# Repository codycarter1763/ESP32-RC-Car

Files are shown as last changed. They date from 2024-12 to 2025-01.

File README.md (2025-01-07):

# DIY ESP32 RC Car

<p align="center">
  
</p>

<h1>Introduction</h1>
Using skills we gained through EE 3752 labs and lectures, my partner and I decided to apply our arm assembly knowledge to microcontrollers and create a fully functional RC car and controller powered by the ESP32. This project connects to ARM assembly and microprocessors by applying embedded system principles like GPIO/ADC handling, I/O, and real time communication. Skills we used in the labs including registers, loops, low-level debugging, and I/O helped us design and fabricate a functional project using the ESP32. This project is very important because it allowed us to take what we learned in class, and apply to a real world application. This connection is like what one would see in a job where you must think outside of the box using your technical skills to solve an issue. 

<h1>Background Information and Design Process</h1>
When we decided to take on this project, we started researching and deciding on what we need to make the RC car reliable, low cost, and fully functional. We chose the ESP32 microcontroller as our processor due to low cost, form factor, adaptability, and Bluetooth and Wi-Fi capabilities. The Xtensa dual-core 32-bit LX6 microprocessor, operating at 240 MHz adds a lot of capability compared to a normal Arduino UNO. The ESP32 also includes peripherals we need without having to buy WI-FI/Bluetooth modules to interface between the car and transmitter externally.

<p align="center">
  
</p>
<!-- -->
Our first iteration of the prototype involved a toy RC car kit on Amazon for our base. 
<p align="center">
  
</p>

Our goal was to have a finished RC car kit that we can place all our electronics on so we would not have to design a chassis. To get this iteration working, we would have to buy an ESP32, and two H-bridge motor drivers for steering and throttle. For the controller we wanted to use a phone app and use ESP32’s Bluetooth capability to control the RC car. This iteration would have worked fine for the scope of this project, but after seeing how fast we would finish the project we came up with a new idea. We wanted to take the RC car a step further and make a faster, more durable, and more custom RC car with a fabricated controller. 
<!-- -->
After research on Thingiverse, we settled on the platform called Carduino V2 and applied our own electronic design using the ESP32 Microcontroller and a brushless motor system. This design did not include any code files so this made it a perfect opportunity to design a system from scratch.

<p align="center">
  
</p>

With the use of a personal 3D printer, we were able to fabricate our own parts without relying on our college’s printers. 
<!-- -->
When we started developing this prototype, we first had trouble with the brushless motor and ESC interface with the ESP32 board. Getting a signal going to the ESC was tricky, the motor would power on and begin beeping in 1 second intervals. Per the instructions for the motor indicated to us that it wasn’t receiving a control signal from the board. Further troubleshooting indicated that the problem was the ESC was waiting for certain throttle calibration steps involving full, low, and neutral throttle. Once we built that functionality into our code, we were able to interface and control the ESC. Thankfully, the steering servo worked right away, it gave us no issues since no calibration is needed. 

<h1>Parts List</h1>
•	2x ESP32<br>
•	1000kv A2212 Brushless Motor 30 amp ESC combo<br>
•	2s 7.4 Volt LIPO<br>
•	SG90 Servos<br>
•	8x12x3.5 Bearings<br>
•	A959 Tire<br>
•	Screws<br>
•	Joysticks and Wires<br>
•	Headers<br>
•	2x Blue LEDs<br>
•	100 Ohm resistor<br>
•	2x Clear White LEDs (For Headlights)<br>
•	68 Ohm resistor<br>

<h1>Chassis Construction</h1>
Chassis construction was relatively simple, the instructions provided with the Carduino 3Dprint files were fairly thorough. The build was broken down into 3 sections; base, steering rack, and rear assembly. <br>
<br>
The rear assembly went together first, this component holds in 4 bearings which support the rear axle and reduce friction when its powered. The brushless motor sits on a mount above the rear assembly, it powers a gear that connects to the rear axle providing motion for the vehicle. The entire construction is held together by 20 M3x10 screws. The rear assembly also supports the wing. The entire assembly is held onto the base with 2 screws forming a hinge-like mechanism, this functions as the suspension for the rear wheels.<br>
<br>
The steering rack was slightly more complex. Each wheel is held by a hub that can rotate left or right depending on the servo mounted in the middle, the hubs are connected to suspension arms that allow for up-and-down movement. Tension is provided to both the front and rear suspension via a set of rubber bands tightly bound around hooks on the suspension arms. <br>
<br>
The base is one single piece with a series of pegs that hold in the battery and the ESP32 board itself. Overall, the chassis went together decently well, the print didn’t include threads for the screws, this made it troublesome to screw everything together as we didn’t have a drill or any other means of forming our own threads. The chassis proved very sturdy and without fault during our testing, it has apt space for all the wiring and saved us a lot of time during the build since we didn’t have to fabricate our own chassis from the ground up. <br>
<br>

<h1>Circuit Design</h1>
For our RC car, this was the circuit diagram that we made that shows our wiring.


<br>
<br>
For our LEDs, we used Ohm’s law to calculate what resistors we needed to use to prevent the LED from burning out.


<br>
<br>
<br>

Our project was gladly sponsored by PCBWay. PCBWay has provided professional solutions to students and electronics enthusiasts, and we believe that their sponsorship would be essential to easy and reliable construction of ESP32 breakout boards for the car and controller. Such boards will allow for removability in case of ESP32 failure or programming, as well as options for different pin assignments. With this breakout board, we could apply to more projects as an easy and reliable way to add a more permanent setup for the ESP32. It’s an honor to share the results with the PCBWay community and contribute our project to their platform.  <br>
 <br>
 
image-asset

<p align="center">
  
</p>

<h1>Code Overview</h1>
Below is a state chart that we wrote up to be able to clearly see the function of the code for specific parts of the program execution. 



<h1>Testing and Design Improvements</h1>
•	During the debugging process, we added various serial monitor outputs at critical parts of the code to see logically why our code was not working. Such techniques, for example, were used to discover what values our joysticks outputted when we moved them. <br> 
•	During our prototyping, we first used WI-FI connectivity for communication between the car and controller. Due to noticeable input lag, we decided to use Bluetooth as the latency is 1-3ms. The disadvantage is the decreased range, but for the safety and reliable use of the system we opted for Bluetooth. <br>
•	During testing, there were cases where the RC car would run away when there was a controller disconnection. As a result, we added in logic to always check for connection from the controller before each iteration. If there was no connection, the ESP32 would send a neutral throttle PWM value to prevent the car from running away.  <br>
•	One issue we ran into was the A959 tires we used non compatible rims to work with our design. After printing out the supplied rims on the Carduino V2 instructions, the rims were slightly too small to fit the tires. So, we made the rim a 2mm bigger diameter on each side and add a small bit of material to the screw hole using a CAD program to account for the screw hole being slightly bigger after increasing rim size.   <br>





•	After prototyping, we fabricated PCB boards to attach our ESP32 with a more permanent and compact form factor. Our intent was to use headers to allow the ESP32 to be removable in case of failure or future programming.  <br>





<h1>Future Design Improvements</h1>
Through the fabrication of the RC car, we found some limitations to our design involving the electronics. Some improvements and solutions we saw to implement in the future are included below.<br>
<br>
•	The ESC we used to control our motor and power the ESP32 is used for drone and plane applications and does not come with reverse and brakes by default. Through much trial and error, we could not program our ESC according to the instructions to add the reverse and braking capability. Our solution would be to buy a dedicated ESC for an RC car, like this.<br>
<br>
•	The range of the ESP32’s Bluetooth is limited as it’s about 30-40 feet in open air compared to hobby grade RC vehicle ranges can span thousands of feet to even kilometers. One way we could fix this limitation is add additional radio transmission hardware such as the NRF24L01+PA+LNA Wireless Transceiver which would increase our range to thousands of feet with very minimal controller latency of 1 to 3ms. This board can adapt very easily through the ESP32 using libraries.<br>
<br>
o	Another solution to increase range would be to use the HopeRF RFM95/96 transceiver system to increase our range to multiple kilometers with low latency. Though for the scope of our project an RC car is not going to need that range normally.<br> 
<br>
•	We found a design online for a shell for our transmitter to house our electronics. The finished ESP32 PCB board we fabricated did not fit completely in our shell. We did not have time for this project, but in the future, we could modify the CAD design and make the controller wider to house our electronics.<br> 
<br>
•	We did not have time before the presentation, but we plan on submitting our project to PCBWay to get a circuit board sponsored very soon. PCBWay very regularly sponsors students and makers around the world to complete their projects with very professional and reliable circuit boards. <br>
<br>
•	Another improvement would be a proper body for the car. This would aid greatly in protecting the fragile internal components of the vehicle against obstacles and collisions.<br>
<br>



•	Another area that could use improvement would be the steering rack, the arms that connect to the servo are stiff and grind against the screw holding the assembly together. One side tends to stick to the screw during compression of the suspension, which could limit steering in the immediate time after a jump. A way to fix this is to use ball ends with a threaded rod, such designs are used on hobby grade RCs to alleviate pressure and grinding through varying suspension travel positions. <br>
<br>

<br>
<h1>Conclusion</h1>
Overall, this was a very challenging but fun project that was very beneficial in applying our lab knowledge to a real-world application. This project connected to ARM assembly and microprocessors by applying embedded system principles like GPIO/ADC handling, I/O, and real time communication. This project took a lot of trial and error to get the car working safely and reliably but using skills we used in the labs involving low level debugging we were able to get a solution. This connection is like what one would see in a job where you must apply prior knowledge to solve an issue. In the future we hope to develop this RC car to be even more reliable and useable and see where this sort of idea can take us.  <br>
<br>
Thanks again to PCBWay for their proud support for our project. PCBWay has provided professional solutions to students and electronics enthusiasts, and we are happy to share what we’ve been building to the PCBWay community and LSU.

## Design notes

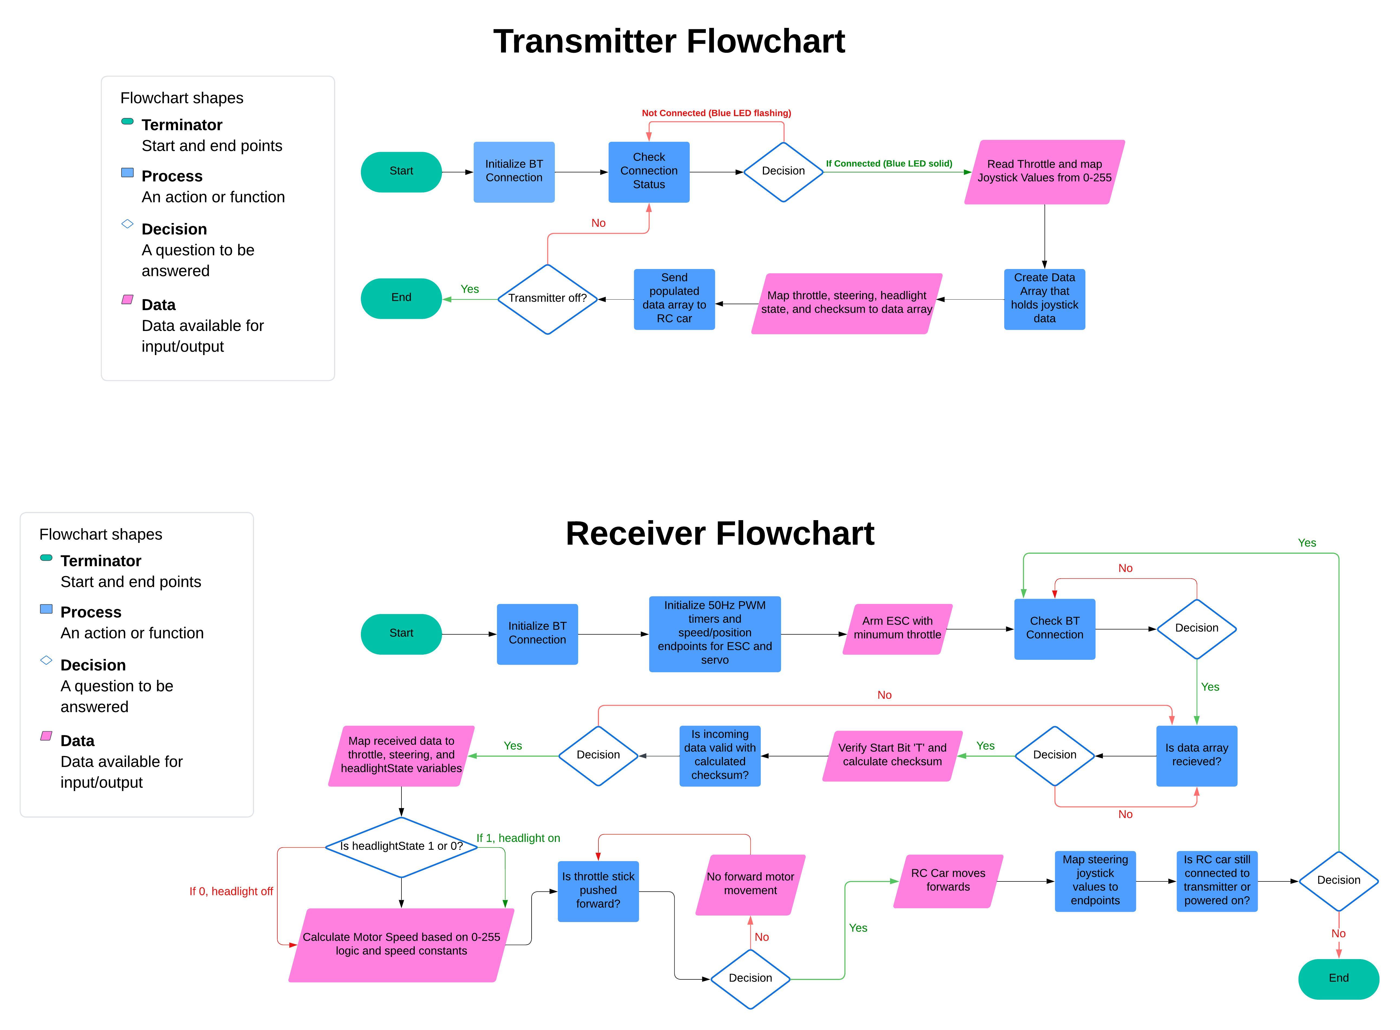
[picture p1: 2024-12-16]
Flowchart.jpeg

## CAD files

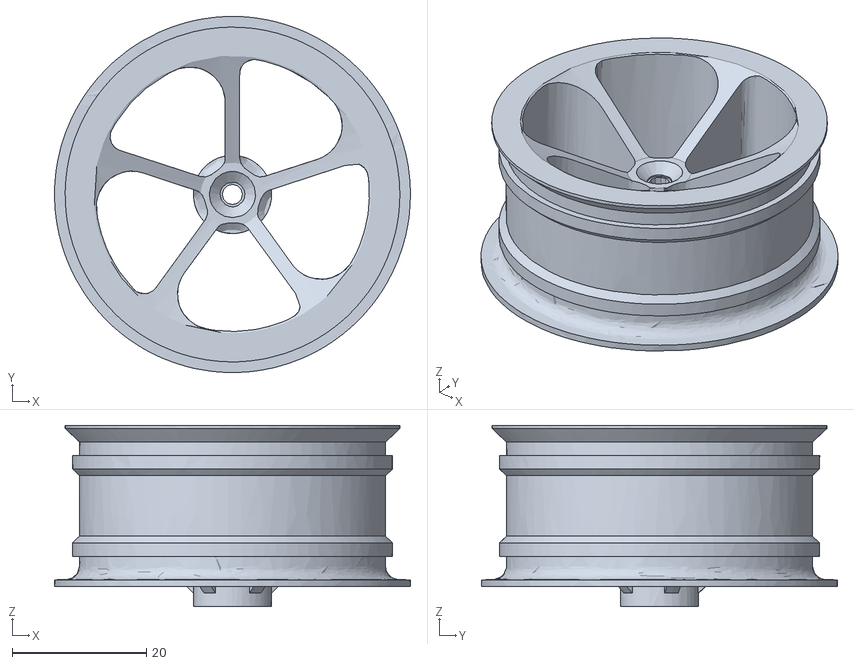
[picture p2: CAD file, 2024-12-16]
Rear Wheel Updated.stl
53.0 x 53.0 x 27.0

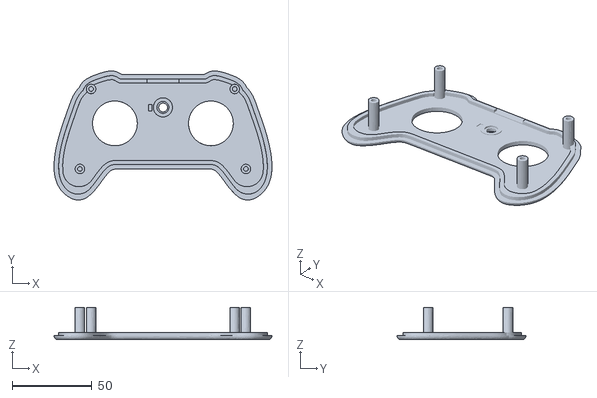
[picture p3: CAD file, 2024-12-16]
Controller 2 Updated.stl
136.3 x 80.6 x 20.3

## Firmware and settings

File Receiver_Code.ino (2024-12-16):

//Reciever Code

#include <BluetoothSerial.h>
#include <ESP32Servo.h>

// Bluetooth server setup
BluetoothSerial SerialBT;

// Servo object for steering and ESC
Servo myservo;
Servo brushlessMotor;

// Pin definitions for motor, servo, and LEDs
#define MOTOR_PWM_PIN 18      // PWM pin for controlling Brushless Motor (ESC)
#define SERVO_PIN 33          // PWM pin for controlling Servo
#define STATUSLEDPIN 2       // Pin for BT status LED
#define HEADLIGHTPIN 13       // Pin for headlights

// Motor control and servo control settings
#define PWM_FREQ 50           // PWM frequency for the motor (ESC)
#define MOTOR_LOW_SPEED 1000  // Minimum speed (full reverse in microseconds)
#define MOTOR_NEUTRAL 1000    // Neutral speed (no movement)
#define MOTOR_HIGH_SPEED 2000 // Maximum speed (full forward in microseconds)

// Speed adjustment constants
const float FORWARD_SPEED_FACTOR = 0.3; // Scale forward speed (0.0 to 1.0)
const float REVERSE_SPEED_FACTOR = 0.5; // Scale reverse speed (0.0 to 1.0)

// Safety timeout variables
#define TIMEOUT_PERIOD 2000   // Timeout period in milliseconds (2 seconds)
unsigned long lastDataTime = 0; // Timestamp of the last valid data

void setup() {
  Serial.begin(115200);
  SerialBT.begin("ESP32_RC_Car"); // Initialize Bluetooth with a device name
  Serial.println("Bluetooth started. Waiting for connection...");

  
  pinMode(STATUSLEDPIN, OUTPUT);
  pinMode(HEADLIGHTPIN, OUTPUT);

  // Allocate PWM timers for ESP32
  ESP32PWM::allocateTimer(0);
  ESP32PWM::allocateTimer(1);
  ESP32PWM::allocateTimer(2);
  ESP32PWM::allocateTimer(3);

  // Initialize brushless motor (ESC)
  brushlessMotor.setPeriodHertz(PWM_FREQ); // Set standard ESC PWM frequency (50 Hz)
  brushlessMotor.attach(MOTOR_PWM_PIN, MOTOR_LOW_SPEED, MOTOR_HIGH_SPEED);

  // Initialize servo for steering
  myservo.setPeriodHertz(PWM_FREQ); // Set standard servo PWM frequency (50 Hz)
  myservo.attach(SERVO_PIN, 600, 2000); // Min and max pulse width for servo

  // ESC Calibration Routine
  Serial.println("Calibrating ESC...");
  
  // Step 1: Send Maximum PWM (Full Forward Throttle)
  Serial.println("Sending full forward throttle...");
  brushlessMotor.writeMicroseconds(MOTOR_HIGH_SPEED);
  delay(2000); // Wait for ESC to register maximum throttle

  // Step 2: Send Minimum PWM (Full Reverse Throttle)
  Serial.println("Sending full reverse throttle...");
  brushlessMotor.writeMicroseconds(MOTOR_LOW_SPEED);
  delay(2000); // Wait for ESC to register minimum throttle

  // Step 3: Send Neutral PWM (No Movement)
  Serial.println("Sending neutral throttle...");
  brushlessMotor.writeMicroseconds(MOTOR_NEUTRAL);
  delay(2000); // Wait for ESC to register neutral position

  Serial.println("ESC Calibration Complete!");
}

void loop() {
  if (SerialBT.hasClient()) {
    Serial.println("Client connected!");
    digitalWrite(STATUSLEDPIN, HIGH); // LED on for successful connection
  } else {
    Serial.println("Waiting for client...");

    // Blink LED for no connection
    digitalWrite(STATUSLEDPIN, HIGH);
    delay(500);
    digitalWrite(STATUSLEDPIN, LOW);
    delay(500);

    // Stop the motor for safety if no client is connected
    brushlessMotor.writeMicroseconds(MOTOR_NEUTRAL);
    myservo.write(90); // Center the steering
    digitalWrite(HEADLIGHTPIN, LOW); // Turn off headlights
    return; // Skip the rest of the loop until a client connects
  }

  // Receives data array from controller
  if (SerialBT.available()) {
    uint8_t recv_data[6];
    SerialBT.readBytes(recv_data, 6);

    // Verify start byte
    if (recv_data[0] != 'T') {
      Serial.println("Invalid data received!");
      return;
    }

    // Calculate checksum
    uint8_t checksum = 0;
    for (int i = 1; i <= 4; i++) {
      checksum += recv_data[i];
    }

    // Check if checksum from controller is valid
    if (recv_data[5] != checksum) {
      Serial.println("Checksum error!");
      return;
    }

    // Update the last valid data timestamp
    lastDataTime = millis();

    // Parse data
    int throttleValue = recv_data[1];
    int steeringValue = recv_data[2];
    int headlightState = recv_data[3];

    // Control headlights
    if (headlightState == 1) {
      digitalWrite(HEADLIGHTPIN, HIGH);
      Serial.println("Headlights On");
    } else {
      digitalWrite(HEADLIGHTPIN, LOW);
      Serial.println("Headlights Off");
    }

    Serial.printf("Throttle: %d | Steering: %d\n", throttleValue, steeringValue);

    // Map throttle value to motor speed (reversed)
    int motorSpeed;
     if (throttleValue < 127) {
      // Reverse motion
      motorSpeed = map(throttleValue, 0, 127, MOTOR_LOW_SPEED, MOTOR_NEUTRAL);
      motorSpeed = MOTOR_NEUTRAL - (MOTOR_NEUTRAL - motorSpeed) * REVERSE_SPEED_FACTOR;
    } else if (throttleValue > 127) {
      // Forward motion
      motorSpeed = map(throttleValue, 127, 255, MOTOR_NEUTRAL, MOTOR_HIGH_SPEED);
      motorSpeed = MOTOR_NEUTRAL + (motorSpeed - MOTOR_NEUTRAL) * FORWARD_SPEED_FACTOR;
    } else {
      // Dead zone (neutral)
      motorSpeed = MOTOR_NEUTRAL;
    }

    // Send the calculated PWM motor speed to the ESC
    brushlessMotor.writeMicroseconds(motorSpeed);

    // Map steering value to servo angle (reversed steering)
    int steeringAngle = map(steeringValue, 0, 255, 180, 0);
    myservo.write(steeringAngle);
  }

  // Safety check: Stop the motor if no valid data received in the timeout period
  if (millis() - lastDataTime > TIMEOUT_PERIOD) {
    Serial.println("Connection lost! Stopping motor and centering steering.");
    brushlessMotor.writeMicroseconds(MOTOR_NEUTRAL); // Stop the motor
    myservo.write(90); // Center the steering
    digitalWrite(HEADLIGHTPIN, LOW); // Turn off headlights
  }
}

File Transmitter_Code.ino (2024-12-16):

#include <BluetoothSerial.h>

// Bluetooth server setup
BluetoothSerial SerialBT;

// Joystick pin definitions
#define THROTTLE_PIN 34  // Throttle (Y-axis)
#define STEERING_PIN 36  // Steering (X-axis)
#define STATUSLEDPIN 33  // BT connection status LED
#define LJOYSTICKBUTTON 26 // Pin for L Joystick switch

int buttonOld = 1;
int buttonNew;
int headlightState = 0;

// Slave MAC address
uint8_t address[6] = {0xC0, 0x5D, 0x89, 0xB0, 0x45, 0xD2}; // MAC address of RC car for BT connection

void setup() {
  Serial.begin(115200);

  // Initialize Bluetooth Serial
  if (!SerialBT.begin("ESP32_Transmitter")) {
    Serial.println("Bluetooth initialization failed!");
    while (1);
  }

  pinMode(THROTTLE_PIN, INPUT);
  pinMode(STEERING_PIN, INPUT);
  pinMode(STATUSLEDPIN, OUTPUT);
  pinMode(LJOYSTICKBUTTON, INPUT_PULLUP);

  // Attempt to connect to RC car
  Serial.println("Attempting to connect to RC car...");
  bool connected = SerialBT.connect(address);

  if (connected) {
    Serial.println("Connected successfully to RC car!");
    digitalWrite(STATUSLEDPIN, HIGH); // Turn on LED when connected
  } else {
    Serial.println("Failed to connect to RC car. Entering blinking mode...");
  }
}
void loop() {
  if (!SerialBT.connected()) {
    // Blink LED if not connected
    digitalWrite(STATUSLEDPIN, HIGH);
    delay(500);
    digitalWrite(STATUSLEDPIN, LOW);
    delay(500);
  } else {
    buttonNew = digitalRead(LJOYSTICKBUTTON);

    // Detect a rising edge (button released when using INPUT_PULLUP)
    if (buttonOld == 1 && buttonNew == 0) {
      // Toggle the LED state
      if (headlightState == 0) {
        headlightState = 1; // On
        Serial.println("Headlights On");
      } else {
        headlightState = 0; // Off
        Serial.println("Headlights Off");
      }
    }
    buttonOld = buttonNew; // Save current state for next iteration

    // Read joystick values
    int throttleRaw = analogRead(THROTTLE_PIN) >> 4; // Map to 0-255
    int steeringRaw = analogRead(STEERING_PIN) >> 4; // Raw steering value
    
    int steeringValue = map(steeringRaw, 0, 255, 127, -128); // Map to 127 to -128 for reversing
    int throttleValue = map(throttleRaw, 0, 255 , 127, -128); // Map to 255 to 0 for reversing

    // Prepare data for sending
    uint8_t send_data[6];
    send_data[0] = 'T';                // Start byte
    send_data[1] = (uint8_t)throttleValue + 128;      // Throttle value
    send_data[2] = (uint8_t)steeringValue + 128; // Adjust to send as unsigned
    send_data[3] = headlightState;     // Headlight value
    send_data[4] = 0;                  // Reserved for future use
    send_data[5] = send_data[1] + send_data[2] + send_data[3]; // Checksum

    SerialBT.write(send_data, 6); // Send data to RC car
    Serial.printf("Sent: Throttle=%d, Steering=%d, HeadlightState=%d\n", throttleValue, steeringValue, headlightState);

    delay(50); // Adjust delay for smoother communication
  }
}
